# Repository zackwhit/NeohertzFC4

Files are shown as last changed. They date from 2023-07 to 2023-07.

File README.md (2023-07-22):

### About
NeohertzFC4 is my version of of a STM32F405 based flight controller, meant to operate quadcopters.
I developed this because I was curious what really went into the development of a flight controller; they seemed like relatively simple 
devices to cost so much. My goal was to develop something relatively simple and low-cost, and so that's why I opted to use the STM32F4 rather than an F7. Other 
open source designs (there aren't many!) aren't easy to interact with or order: they aren't in KiCAD and aren't on GitHub/Gitlab. So another one of my goals was to
provide a sort of template that would not only make my own development easier, but make it easier for other people as well. 

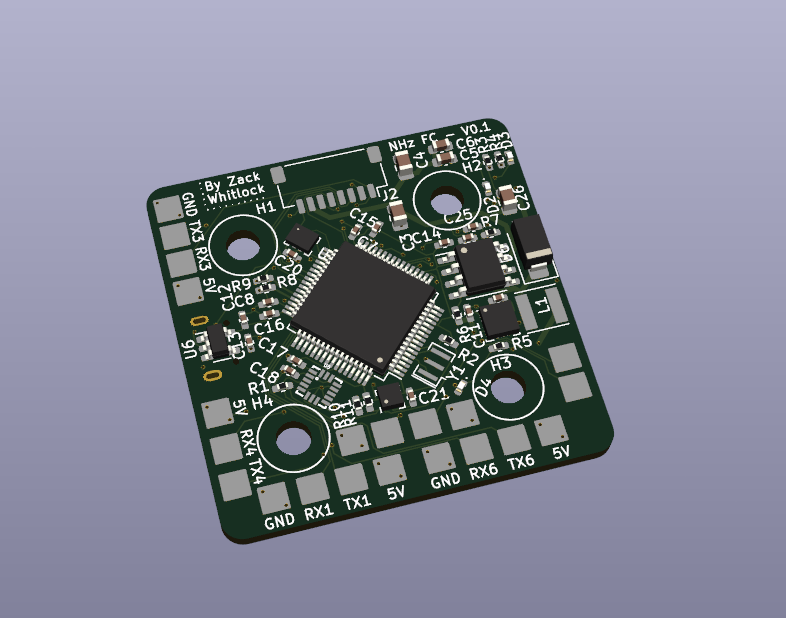
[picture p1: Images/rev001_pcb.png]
plot


#### Features
- STM32F405RGTx main computing chip
- BMP280 barometer
- MMA8452QR1 accelerometer
- LIS3MDL magnometer
- AT7456 analog OSD chip
  
Bonus: LIS3DH accelerometer included as well, since I wanted to add support for it in betaflight. It doesn't have to be populated

### Updates
- July 19th, 2023: I ordered the parts for the first 5 prototypes after working on the design for about a week. All the parts should be here in about two weeks.

### Known Issues
- The JLCPCB information isn't exactly correct in REV001, I would not recomend ordering it at this stage unless you know what you're doing.

### Potential issues
- There aren't many (if any at all) alternative parts for certain ICs. If one were to go out of stock, a small redesign would have to be done to use a different solution.
- As of right now, the hardware is completely untested.

### How to build one!
- Order the PCBs through JLCPCB, I recomend only having them populate the passive components for you at this stage of the project.
- Order your components; I suggest through LCSC
- Assemble! This is a double sided PCB, but you can ignore the bottom side if you don't want to use the analog OSD chip included there.
- Profit.

### Future plans
As of the first revision, there is only one onboard BEC. This means there is only a 5V rail and no 9v (or 10v/12v) rails for a digital 
video system. I am planning on adding a second BEC for that purpose, but it didn't fit with my initial goal of having all the core components on
the top of the PCB. 

I'm also interested in creating a version of this with an AT32 chip instead of an STM32. As far as I can tell they are cheaper, but not necessarily more
available. I'm inclined to making a board that can have either an AT32 or an STM32 chip, that way you could just select whichever one is best at the time. 
Of course, this hinges on betaflight actually having decent support for AT32 chips, since I don't personally have time to add support. 

Other (optional) features I'm interested in adding:
- ELRS receiver built-in, both 900MHz and 2.4GHz options would be great so as to support long range flying.

#### License
GNU General Public License v3.0

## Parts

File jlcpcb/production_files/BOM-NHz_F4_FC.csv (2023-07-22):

Comment | Designator | Footprint | LCSC
75 | R12,R13 | R_0402_1005Metric_Pad0.72x0.64mm_HandSolder | C114757
10k | R1,R2,R6 | R_0402_1005Metric_Pad0.72x0.64mm_HandSolder | C11616
2.2uF | C7,C8 | C_0402_1005Metric_Pad0.74x0.62mm_HandSolder | C12530
47uF | C23,C24 | C_0603_1608Metric_Pad1.08x0.95mm_HandSolder | C140782
100nF | C1,C18,C2,C22,C6,C9 | C_0402_1005Metric_Pad0.74x0.62mm_HandSolder | C1525
1k | R3,R4,R5 | R_0402_1005Metric_Pad0.72x0.64mm_HandSolder | C1527
10uF | C11,C12,C13,C14,C15,C16 | C_0402_1005Metric_Pad0.74x0.62mm_HandSolder | C15525
1uF | C5 | C_0603_1608Metric | C15849
2.2k | R10,R11 | R_0402_1005Metric_Pad0.72x0.64mm_HandSolder | C25879
3.3k | R7 | R_0402_1005Metric_Pad0.72x0.64mm_HandSolder | C25890
100p | C25,D6 | C_0402_1005Metric_Pad0.74x0.62mm_HandSolder | C3018525
22 | R8,R9 | R_0402_1005Metric_Pad0.72x0.64mm_HandSolder | C325383
LED | D3 | LED_0402_1005Metric | C434447
LED | D2 | LED_0402_1005Metric | C434448
4.7uF | C26,C3,C4 | C_0805_2012Metric | C76651
LED | D4 | LED_0402_1005Metric | C965790
4.7uF | C17,C19,C20,C21 | C_0402_1005Metric_Pad0.74x0.62mm_HandSolder | C98192
XC6219B332MR | U6 | SOT-23-5
LIS3DH | U4 | LGA-16_3x3mm_P0.5mm_LayoutBorder3x5y
TestPoint | TP2 | SolderPad_2.5x2.5
22uH | L1 | L_Vishay_IFSC-1515AH_4x4x1.8mm
MountingHole | H2 | MountingHole_3.2mm_M3
TestPoint | TP24 | SolderPad_2.5x2.5
TestPoint | TP20 | SolderPad_2.5x2.5
TestPoint | TP17 | SolderPad_2.5x2.5
TestPoint | TP23 | SolderPad_2.5x2.5
MountingHole | H4 | MountingHole_3.2mm_M3
TestPoint | TP28 | SolderPad_2.5x2.5
BMP280 | U3 | Bosch_LGA-8_2x2.5mm_P0.65mm_ClockwisePinNumbering
MountingHole | H1 | MountingHole_3.2mm_M3
TestPoint | TP27 | SolderPad_2.5x2.5
TestPoint | TP26 | SolderPad_2.5x2.5
TestPoint | TP10 | SolderPad_2.5x2.5
TestPoint | TP13 | SolderPad_2.5x2.5
MountingHole | H3 | MountingHole_3.2mm_M3
TestPoint | TP14 | SolderPad_2.5x2.5
TestPoint | TP11 | SolderPad_2.5x2.5
CSTCE8M00G52-R0 | Y1 | Resonator_SMD_Murata_CSTxExxV-3Pin_3.0x1.1mm
TestPoint | TP16 | SolderPad_2.5x2.5
TestPoint | TP1 | SolderPad_2.5x2.5
TestPoint | TP21 | SolderPad_2.5x2.5
Conn_01x08_Socket | J2 | JST_SH_SM08B-SRSS-TB_1x08-1MP_P1.00mm_Horizontal
TestPoint | TP8 | SolderPad_2.5x2.5
TPS5420D | U2 | SOIC-8_3.9x4.9mm_P1.27mm
STM32F405RGTx | U1 | LQFP-64_10x10mm_P0.5mm
TestPoint | TP15 | SolderPad_2.5x2.5
TestPoint | TP9 | SolderPad_2.5x2.5
TestPoint | TP19 | SolderPad_2.5x2.5
MMA8452QR1 | U5 | QFN-16_0.5MM
TestPoint | TP7 | SolderPad_2.5x2.5
TestPoint | TP12 | SolderPad_2.5x2.5
LIS3MDL | U7 | LGA-12_2x2mm_P0.5mm
TestPoint | TP30 | SolderPad_2.5x2.5
TestPoint | TP5 | SolderPad_2.5x2.5
USB_B_Micro | J1 | USB_Micro-B_XKB_U254-051T-4BH83-F1S
D_Small | D5 | D_SOD-323F
TestPoint | TP4 | SolderPad_2.5x2.5
TestPoint | TP6 | SolderPad_2.5x2.5
TestPoint | TP3 | SolderPad_2.5x2.5
TestPoint | TP25 | SolderPad_2.5x2.5
D_TVS | D1 | D_SMA
TestPoint | TP32 | SolderPad_2.5x2.5
TestPoint | TP29 | SolderPad_2.5x2.5
TestPoint | TP18 | SolderPad_2.5x2.5
Crystal_GND24 | Y3 | Crystal_SMD_2016-4Pin_2.0x1.6mm
TestPoint | TP31 | SolderPad_2.5x2.5
TestPoint | TP22 | SolderPad_2.5x2.5
AT7456 | U8 | TSSOP-28_4.4x9.7mm_P0.65mm
SW_Push | SW2 | SolderJumper-2_P1.3mm_Open_Pad1.0x1.5mm
SW_Push | SW1 | SolderJumper-2_P1.3mm_Open_Pad1.0x1.5mm

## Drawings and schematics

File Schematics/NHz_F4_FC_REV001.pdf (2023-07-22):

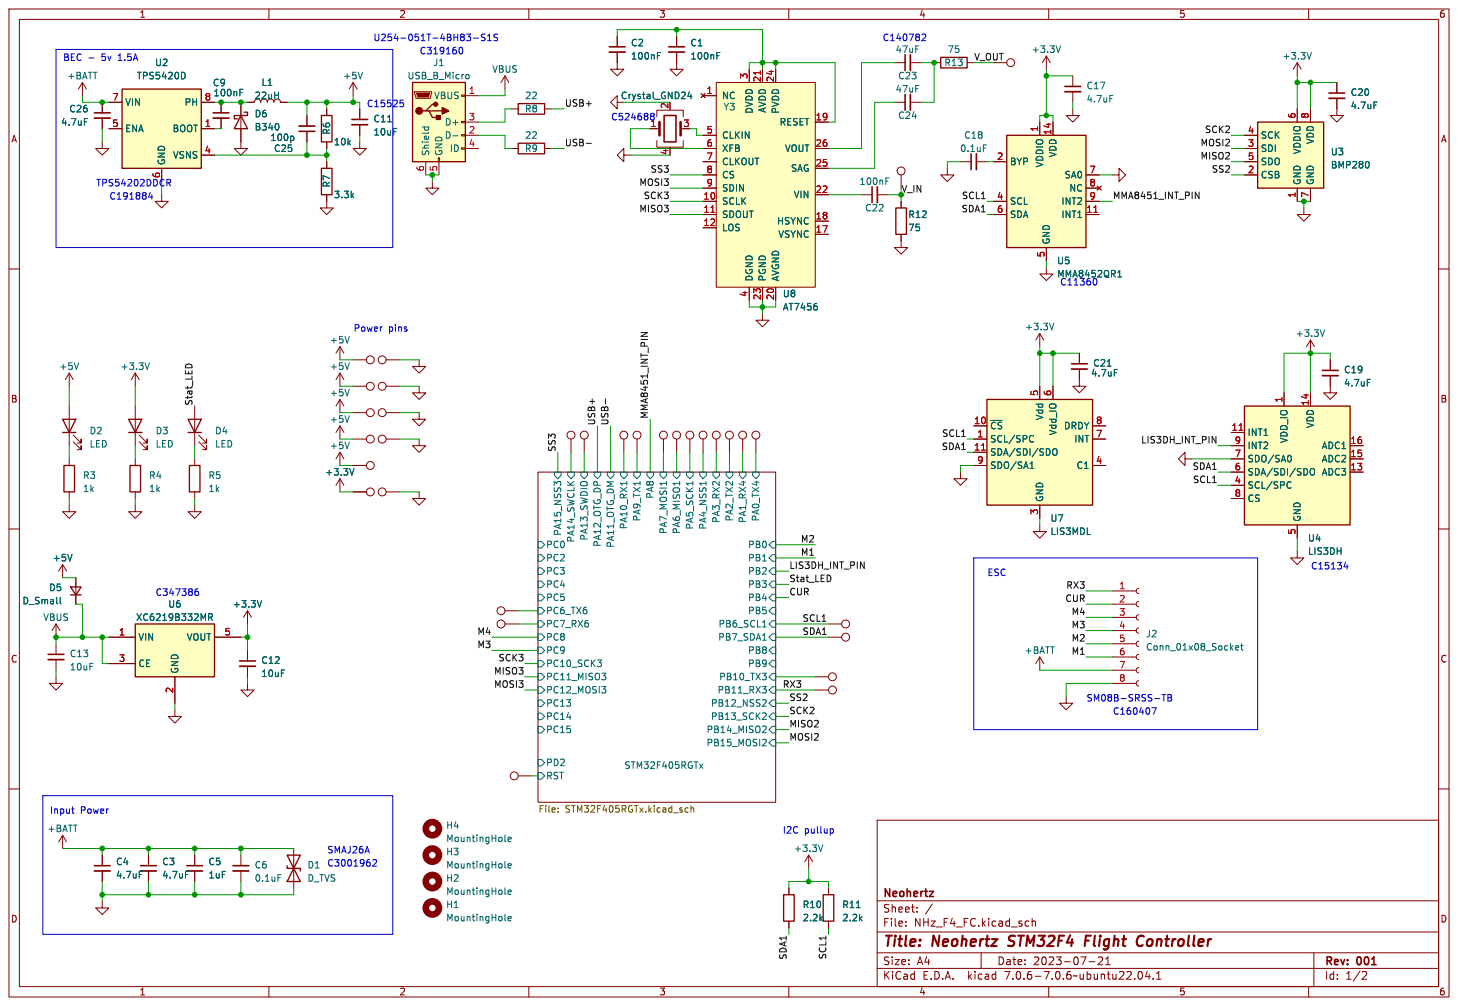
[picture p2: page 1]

4 CLKIN 5 XFB 6 CLKOUT 7 CS 8 SDIN 9 C1
NC 1 SCLK 10 SDOUT 11

4 Y3 Crystal_GND24 +BATT SCL/SPC 1 ~{CS} 10 SDA/SDI/SDO 11 GND

4 CLKIN 5 XFB 6 CLKOUT 7 CS 8 SDIN 9 U8AT7456 D1 D_TVS

1 CSB 2 SDI 3 SCK 4 SDO 5 VDDIO

5 SDA/SDI/SDO 6 SDO/SA0 7 CS 8

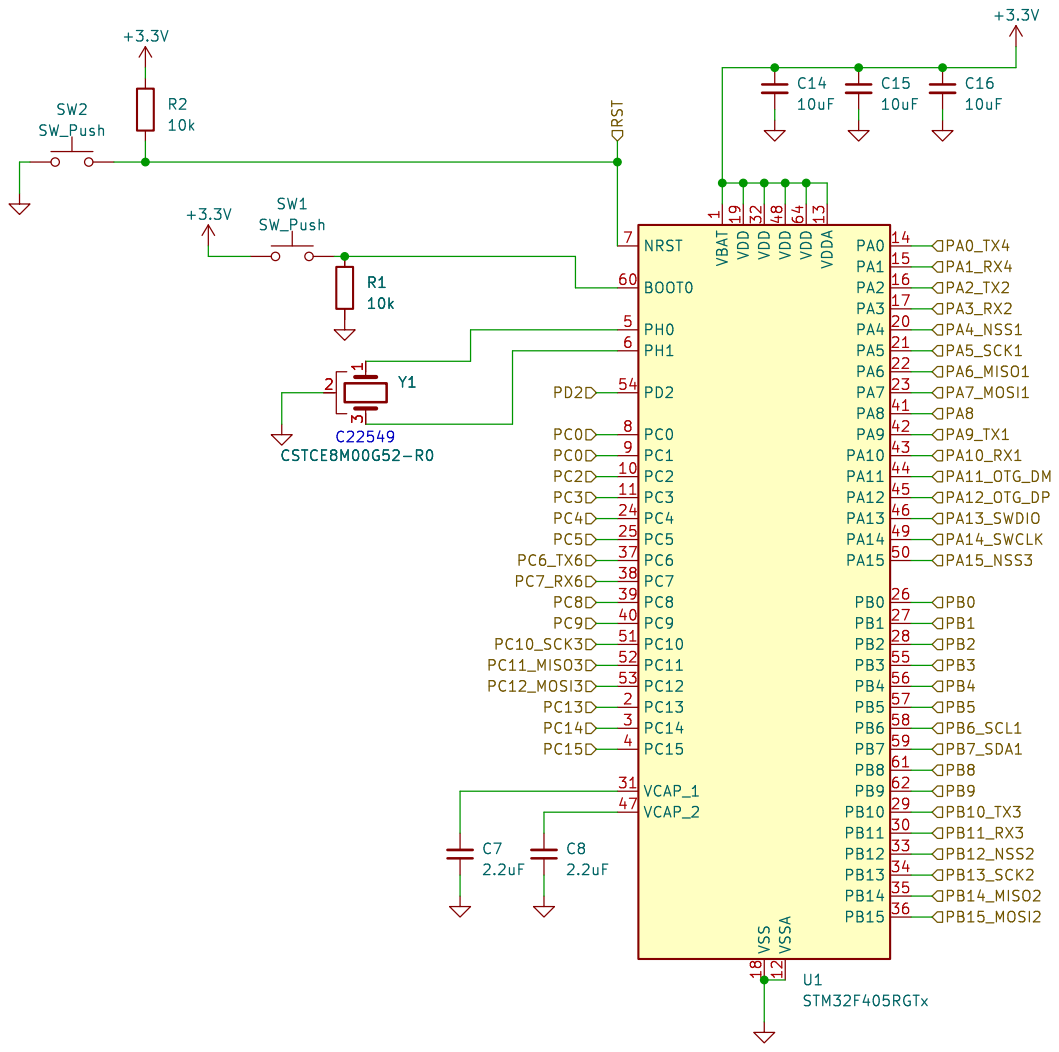
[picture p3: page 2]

Id: 2/2 Title: Neohertz STM32F4 Flight Controller File: STM32F405RGTx.kicad_sch Sheet: /STM32F405RGTx/ Neohertz

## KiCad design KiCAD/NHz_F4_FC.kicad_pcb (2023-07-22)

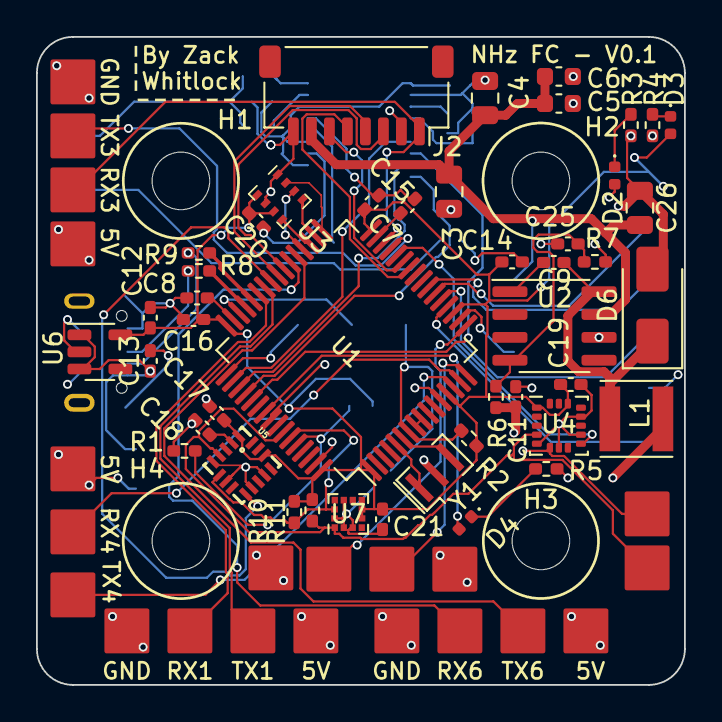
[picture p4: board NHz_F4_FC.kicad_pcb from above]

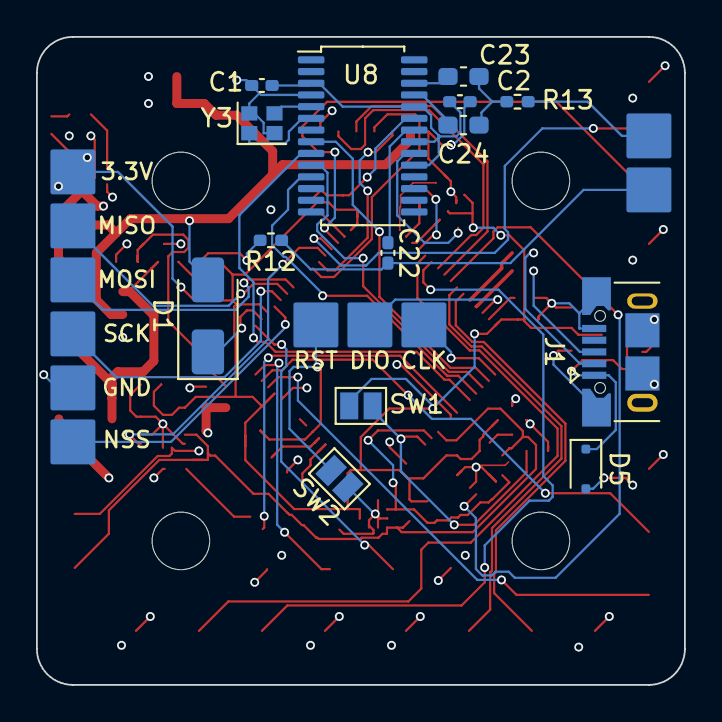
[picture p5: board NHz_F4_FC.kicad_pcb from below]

Board: 4 copper layers, 36.0 x 36.0 mm, 95 parts (25 on the bottom side), 66 nets.

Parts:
C1, C2, C9, C22: 100nF; C_0402_1005Metric_Pad0.74x0.62mm_HandSolder
C3, C4, C26: 4.7uF; C_0805_2012Metric
C5: 1uF; C_0603_1608Metric
C6: 0.1uF; C_0603_1608Metric
C7, C8: 2.2uF; C_0402_1005Metric_Pad0.74x0.62mm_HandSolder
C11, C12, C13, C14, C15, C16: 10uF; C_0402_1005Metric_Pad0.74x0.62mm_HandSolder
C17, C19, C20, C21: 4.7uF; C_0402_1005Metric_Pad0.74x0.62mm_HandSolder
C18: 0.1uF; C_0402_1005Metric_Pad0.74x0.62mm_HandSolder
C23, C24: 47uF; C_0603_1608Metric_Pad1.08x0.95mm_HandSolder
C25: 100p; C_0402_1005Metric_Pad0.74x0.62mm_HandSolder
D1: D_TVS; D_SMA
D2, D3, D4: LED; LED_0402_1005Metric
D5: D_Small; D_SOD-323F
D6: B340; D_SMA
H1, H2, H3, H4: MountingHole; MountingHole_3.2mm_M3
J1: USB_B_Micro; USB_Micro-B_XKB_U254-051T-4BH83-F1S
J2: Conn_01x08_Socket; JST_SH_SM08B-SRSS-TB_1x08-1MP_P1.00mm_Horizontal
L1: 22uH; L_Vishay_IFSC-1515AH_4x4x1.8mm
R1, R2, R6: 10k; R_0402_1005Metric_Pad0.72x0.64mm_HandSolder
R3, R4, R5: 1k; R_0402_1005Metric_Pad0.72x0.64mm_HandSolder
R7: 3.3k; R_0402_1005Metric_Pad0.72x0.64mm_HandSolder
R8, R9: 22; R_0402_1005Metric_Pad0.72x0.64mm_HandSolder
R10, R11: 2.2k; R_0402_1005Metric_Pad0.72x0.64mm_HandSolder
R12, R13: 75; R_0402_1005Metric_Pad0.72x0.64mm_HandSolder
SW1, SW2: SW_Push; SolderJumper-2_P1.3mm_Open_Pad1.0x1.5mm
TP1, TP2, TP3, TP4, TP5, TP6, TP7, TP8, TP9, TP10, TP11, TP12, TP13, TP14, TP15, TP16, TP17, TP18, TP19, TP20, TP21, TP22, TP23, TP24, TP25, TP26, TP27, TP28, TP29, TP30, TP31, TP32: TestPoint; SolderPad_2.5x2.5
U1: STM32F405RGTx; LQFP-64_10x10mm_P0.5mm
U2: TPS5420D; SOIC-8_3.9x4.9mm_P1.27mm
U3: BMP280; Bosch_LGA-8_2x2.5mm_P0.65mm_ClockwisePinNumbering
U4: LIS3DH; LGA-16_3x3mm_P0.5mm_LayoutBorder3x5y
U5: MMA8452QR1; QFN-16_0.5MM
U6: XC6219B332MR; SOT-23-5
U7: LIS3MDL; LGA-12_2x2mm_P0.5mm
U8: AT7456; TSSOP-28_4.4x9.7mm_P0.65mm
Y1: CSTCE8M00G52-R0; Resonator_SMD_Murata_CSTxExxV-3Pin_3.0x1.1mm
Y3: Crystal_GND24; Crystal_SMD_2016-4Pin_2.0x1.6mm

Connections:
+3.3V: C12.1, C14.1, C15.1, C16.1, C17.1, C19.1, C20.1, C21.1, D3.2 (A), R2.1, R10.2, R11.2, SW1.1, TP18.1, U1.1 (VBAT), U1.13 (VDDA), U1.19 (VDD), U1.32 (VDD), U1.48 (VDD), U1.64 (VDD), U3.6 (VDDIO), U3.8 (VDD), U4.1 (VDD_IO), U4.14 (VDD), U5.1 (VDDIO), U5.14 (VDD), U6.5 (VOUT), U7.5 (Vdd), U7.6 (Vdd_IO)
+5V: C11.1, C25.2, D2.2 (A), D5.2 (A), L1.2, R6.1, TP17.1, TP19.1, TP20.1, TP26.1, TP28.1
+BATT: C3.1, C4.1, C5.1, C6.1, C26.1, D1.2 (A2), J2.7, U2.7 (VIN)
/CUR: J2.2, U1.56 (PB4)
/LIS3DH_INT_PIN: U1.28 (PB2), U4.9 (INT2)
/M1: J2.6, U1.27 (PB1)
/M2: J2.5, U1.26 (PB0)
/M3: J2.4, U1.40 (PC9)
/M4: J2.3, U1.39 (PC8)
/MISO2: U1.35 (PB14), U3.5 (SDO)
/MISO3: U1.52 (PC11), U8.11 (SDOUT)
/MMA8451_INT_PIN: U1.41 (PA8), U5.9 (INT2)
/MOSI2: U1.36 (PB15), U3.3 (SDI)
/MOSI3: U1.53 (PC12), U8.9 (SDIN)
/RX3: J2.1, TP14.1, U1.30 (PB11)
/SCK2: U1.34 (PB13), U3.4 (SCK)
/SCK3: U1.51 (PC10), U8.10 (SCLK)
/SCL1: R11.1, TP11.1, U1.58 (PB6), U4.4 (SCL/SPC), U5.4 (SCL), U7.1 (SCL/SPC)
/SDA1: R10.1, TP12.1, U1.59 (PB7), U4.6 (SDA/SDI/SDO), U5.6 (SDA), U7.11 (SDA/SDI/SDO)
/SS2: U1.33 (PB12), U3.2 (CSB)
/SS3: U1.50 (PA15), U8.8 (CS)
/STM32F405RGTx/PA0_TX4: TP10.1, U1.14 (PA0)
/STM32F405RGTx/PA1_RX4: TP9.1, U1.15 (PA1)
/STM32F405RGTx/PA2_TX2: TP8.1, U1.16 (PA2)
/STM32F405RGTx/PA3_RX2: TP7.1, U1.17 (PA3)
/STM32F405RGTx/PA4_NSS1: TP6.1, U1.20 (PA4)
/STM32F405RGTx/PA5_SCK1: TP5.1, U1.21 (PA5)
/STM32F405RGTx/PA6_MISO1: TP4.1, U1.22 (PA6)
/STM32F405RGTx/PA7_MOSI1: TP3.1, U1.23 (PA7)
/STM32F405RGTx/PA9_TX1: TP2.1, U1.42 (PA9)
/STM32F405RGTx/PA10_RX1: TP1.1, U1.43 (PA10)
/STM32F405RGTx/PA13_SWDIO: TP30.1, U1.46 (PA13)
/STM32F405RGTx/PA14_SWCLK: TP29.1, U1.49 (PA14)
/STM32F405RGTx/PB10_TX3: TP13.1, U1.29 (PB10)
/STM32F405RGTx/PC0: U1.8 (PC0), U1.9 (PC1)
/STM32F405RGTx/PC6_TX6: TP16.1, U1.37 (PC6)
/STM32F405RGTx/PC7_RX6: TP15.1, U1.38 (PC7)
/STM32F405RGTx/RST: R2.2, SW2.2, TP25.1, U1.7 (NRST)
/Stat_LED: D4.2 (A), U1.55 (PB3)
/USB+: R8.2, U1.45 (PA12)
/USB-: R9.1, U1.44 (PA11)
/V_IN: C22.2, R12.1, TP31.1
/V_OUT: R13.2, TP32.1
GND: C1.2, C2.2, C3.2, C4.2, C5.2, C6.2, C7.1, C8.1, C11.2, C12.2, C13.2, C14.2, C15.2, C16.2, C17.2, C18.1, C19.2, C20.2, C21.2, C26.2, D1.1 (A1), D6.2 (A), J1.5 (GND), J1.6 (Shield), J2.8, R1.2, R3.2, R4.2, R5.2, R7.2, R12.2, SW2.1, TP21.1, TP22.1, TP23.1, TP24.1, TP27.1, U1.12 (VSSA), U1.18 (VSS), U1.63 (VSS), U2.6 (GND), U3.1 (GND), U3.7 (GND), U4.5 (GND), U4.7 (SDO/SA0), U4.10 (GND), U4.12 (GND), U5.5 (GND), U5.7 (SA0), U5.10 (GND), U5.12 (GND), U6.2 (GND), U7.2 (GND), U7.3 (GND), U7.9 (SDO/SA1), U7.12 (GND), U8.4 (DGND), U8.20 (AVGND), U8.23 (PGND), Y1.2, Y3.2, Y3.4
unnamed: C23.2, C24.2, R13.1
unnamed: D2.1 (K), R3.1
unnamed: D3.1 (K), R4.1
unnamed: D4.1 (K), R5.1
unnamed: C9.1, D6.1 (K), L1.1, U2.8 (PH)
unnamed: J1.3 (D+), R8.1
unnamed: J1.2 (D-), R9.2
unnamed: R1.1, SW1.2, U1.60 (BOOT0)
unnamed: U1.5 (PH0), Y1.1
unnamed: U1.6 (PH1), Y1.3
unnamed: C7.2, U1.31 (VCAP_1)
unnamed: C8.2, U1.47 (VCAP_2)
unnamed: C9.2, U2.1 (BOOT)
unnamed: C25.1, R6.2, R7.1, U2.4 (VSNS)
unnamed: C18.2, U5.2 (BYP)
unnamed: C1.1, C2.1, U8.3 (DVDD), U8.19 (RESET), U8.21 (AVDD), U8.24 (PVDD)
unnamed: U8.5 (CLKIN), Y3.3
unnamed: C24.1, U8.25 (SAG)
unnamed: C22.1, U8.22 (VIN)
unnamed: C23.1, U8.26 (VOUT)
unnamed: U8.6 (XFB), Y3.1
VBUS: C13.1, D5.1 (K), J1.1 (VBUS), U6.1 (VIN), U6.3 (CE)
